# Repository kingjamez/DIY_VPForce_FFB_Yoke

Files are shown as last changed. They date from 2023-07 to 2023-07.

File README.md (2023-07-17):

# DIY VPForce FFB Yoke
This will be a flight control yoke based on the VPForce Force Feedback Motor System. It's not finished, it's barely started. Use any files here at risk of life and liberty!

This can be used as a standard Cessna / Piper style yoke or also easily adapted to use the Cirrus style side yoke. The only difference will be what you attach to the shaft coming out of the device and where you mount it. I think Cirrus drivers will love it.

It's core will be a section of 8020 aluminum extrusion linear rail. 
The roll axis will be direct drive from an 86BLF04 VPForce motor. A honeycomb alpha yoke will be donating it's controls. I hope to use a shift register to have the yoke talk to the VPForce USB interface. 

The pitch axis will be belt or rack and pinion driven from a 57BLF03 VPForce motor. This is TBD since I very  much want this to be as smooth as possible without sacrificing torque. First tests will be standard 2GT-2mm timing belt just like an Ender 3 X-Axis movement. 2nd tests will be 3GT-3mm endless belt. 3rd Test will be rack and pinion using 3D printed gears. The objective is smooth motion (don't want to waste the anti-cogging that is so well implimented by VPForce). All tests will likely utilize the inertia feature in the VPForce software to give smooth pitch motion.

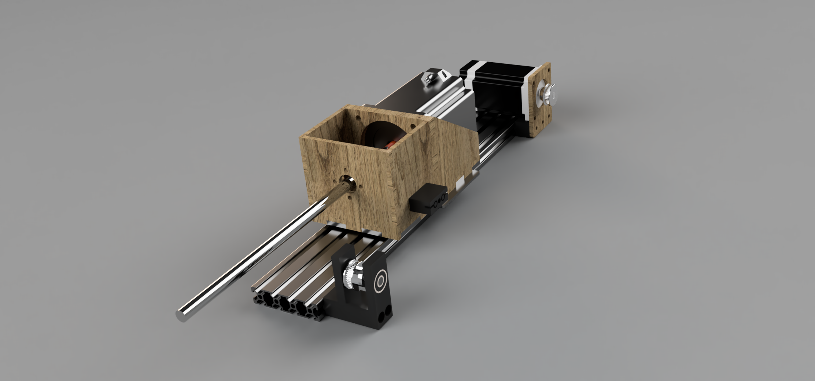
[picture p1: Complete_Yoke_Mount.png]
 

The above box houses the 86BLF04 motor and a shaft coupler to attach the 12mm shaft through a LM12UU linear bearing. This laser cut box will bolt to an aluminum gantry plate and ride along a section of 8020x400mm rail. Here is a link to the rail: https://a.co/d/cz4xqeC 

The gantry plate also came from Amazon but you can cut one out along with the other parts. https://a.co/d/fDJAr2g .
I eventually plan to merge the gantry plate and the bottom of the motor mounting box into one piece. However the width of the 86BLF04 motor matches very well with the location of the holes for the bolts that hold the wheels so I decided to tackle that problem in V2. V1 will require the gantry plate and the motor mount box will just bolt to the gantry plate. 

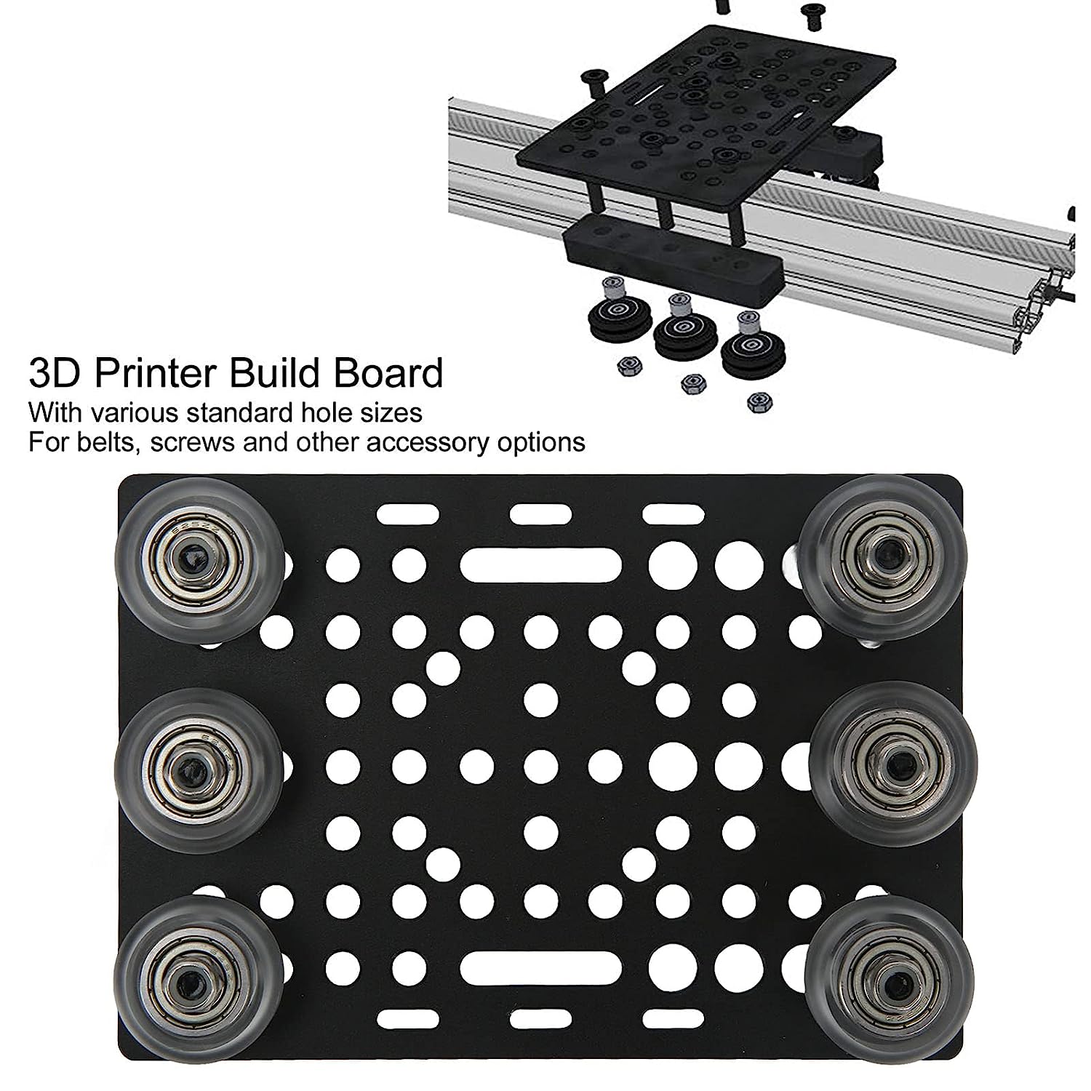
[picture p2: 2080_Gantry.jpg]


This is the 8020 rail: 
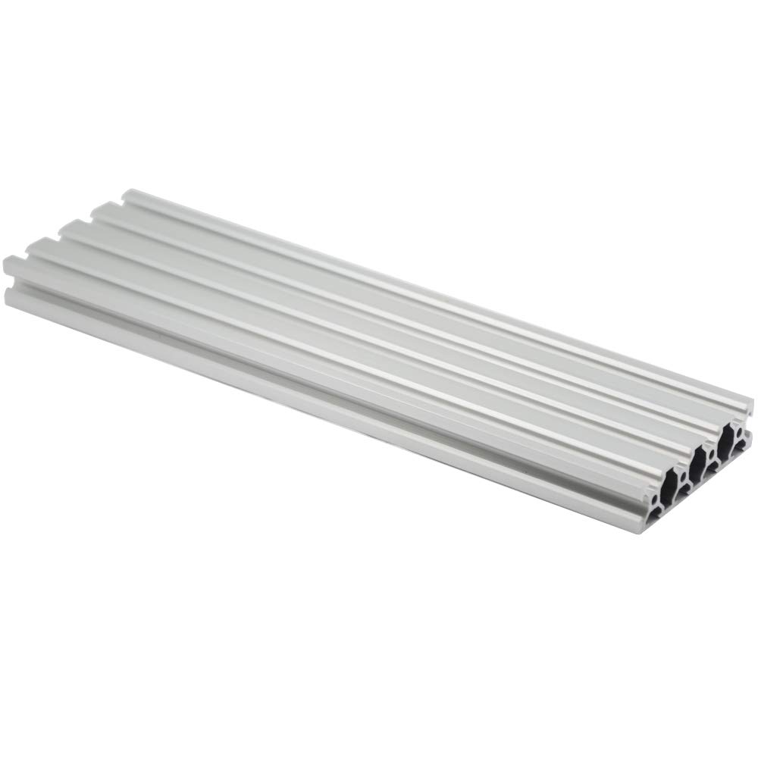
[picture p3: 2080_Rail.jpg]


This project is just getting started, more to come shortly.

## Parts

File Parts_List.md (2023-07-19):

Parts list for FFB Yoke
Motors and motor control board from VPForce:
1x86BLF04, 1x57BLF03, 1x USB control board.
8020x400mm rail. I sourced from Amazon.
Laser cut wood carraige: All DXF's laser cut out of 1/4" (nominal, US 1/4" plywood is 5.35mm) plywood or equivilant. 
3D Printed parts:
1x Rear servo mount
1x Front Idler mount
1x Belt Clamp
1x Belt Clamp nut holder
1x VPForce control board holder

1x Yoke of your choosing. I used a Honeycomb Alpha as a donor. It has a nice yoke that has a 12mm shaft that makes connecting to the 86BLF04 easy.
1x 12.7mm to 12mm shaft coupling to go between motor and yoke shaft.
2x LM12UU Flanged Linear bearings for yoke shaft support.
8x 6mmx25mm bolts for mounting the servo motors.
1x 6mm tap to tap the holes in the 86FLB04 motor to M6 (they come unthreaded).
8x M4x15mm bolts and nuts to secure the LM12UU linear bearings.
2x M5x45mm bolts for the rear servo mount.
2x M5x55mm bolts for the front idler holder.
1x M5x55mm bolt for the belt clamp (this may change)
1x M55 nut for belt clamp.

Wood glue to hold carriage together.
1x 8020 Gantry plate with hardware and 6 wheels. Ensure that it has eccentric spacers for close tolerance rail movement.
4x M4xxx bolts to hold wooden carraige to above 8020 aluminum carriage.

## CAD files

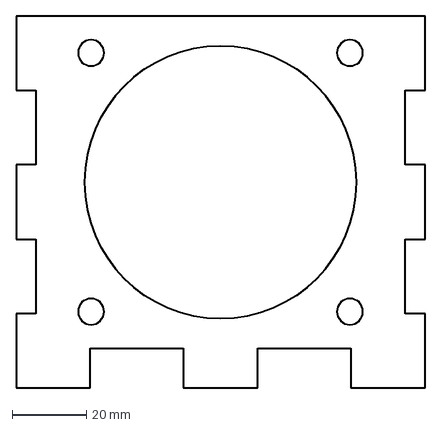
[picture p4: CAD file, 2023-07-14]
dxf/6BLF04_Center_Mount.dxf
110.0 x 100.0 mm

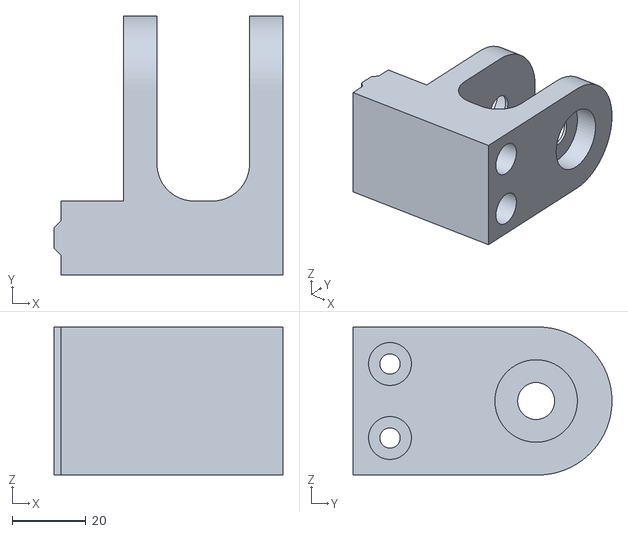
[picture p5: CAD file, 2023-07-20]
STLs/Roller_Pillow_Rail_Mount v7.stl
61.8 x 70.0 x 40.0

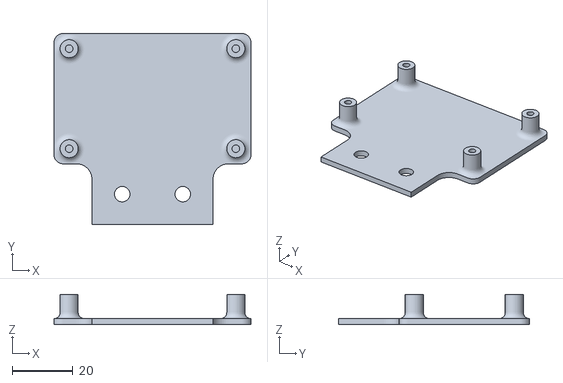
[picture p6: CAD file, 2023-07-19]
VPForce_rail_Board_Holder v3.stl
65.0 x 63.0 x 10.0

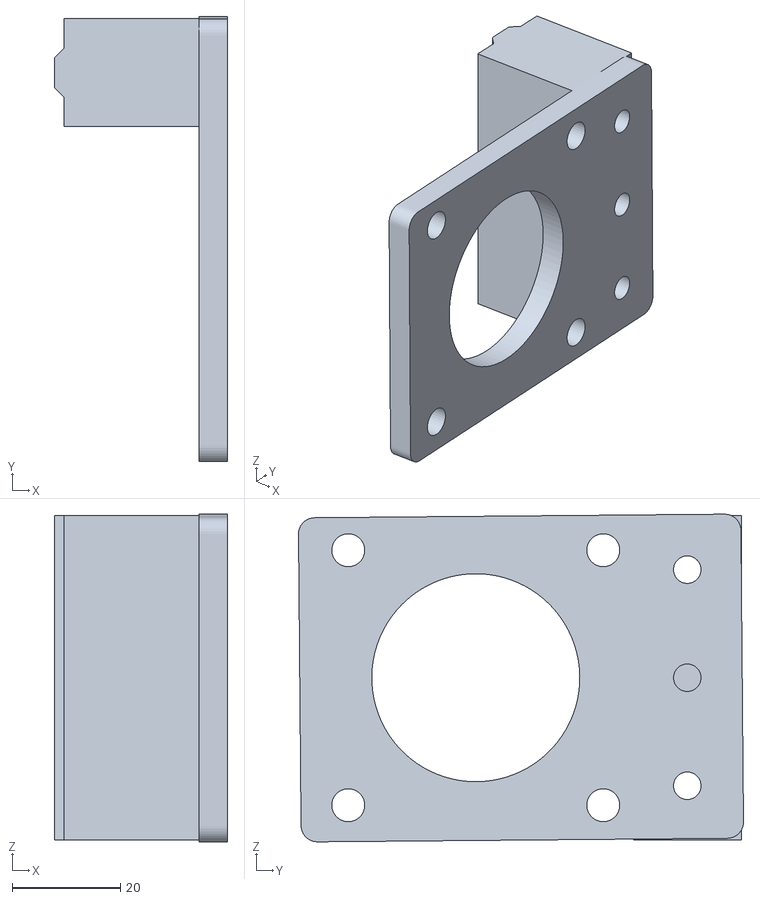
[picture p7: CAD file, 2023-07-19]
Combind_Nema23.stl
32.1 x 82.4 x 60.7

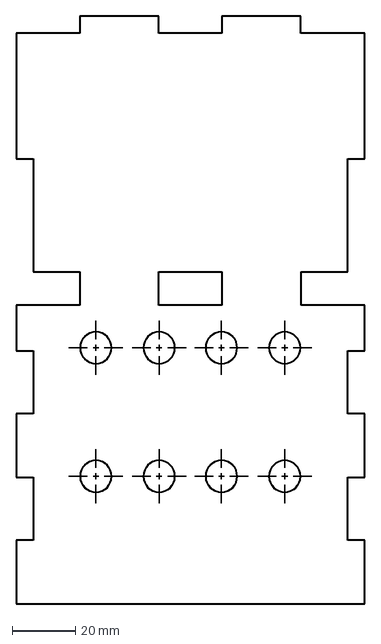
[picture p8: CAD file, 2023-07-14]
dxf/Bottom_Panel_Top_Center_Marked.dxf
110.0 x 185.7 mm

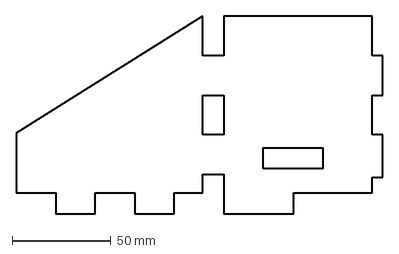
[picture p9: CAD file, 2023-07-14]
dxf/Side_Support.dxf
185.4 x 100.0 mm

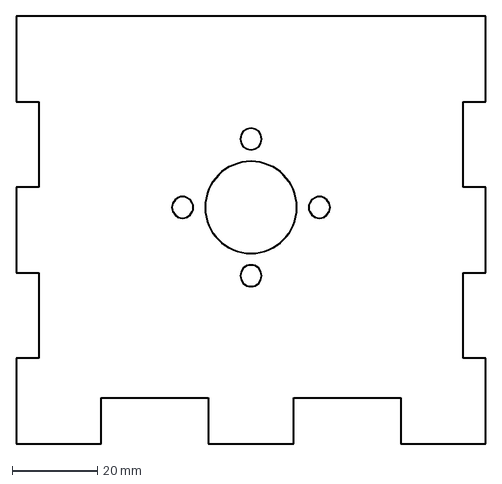
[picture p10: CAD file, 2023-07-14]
dxf/Front_Support.dxf
110.0 x 100.0 mm

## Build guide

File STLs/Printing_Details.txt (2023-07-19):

I printed these out of CF-PETG but I suspect that almost any filament will work well. 
The rear servo mount might benefit from a high-temp filament because that motor gets warm.

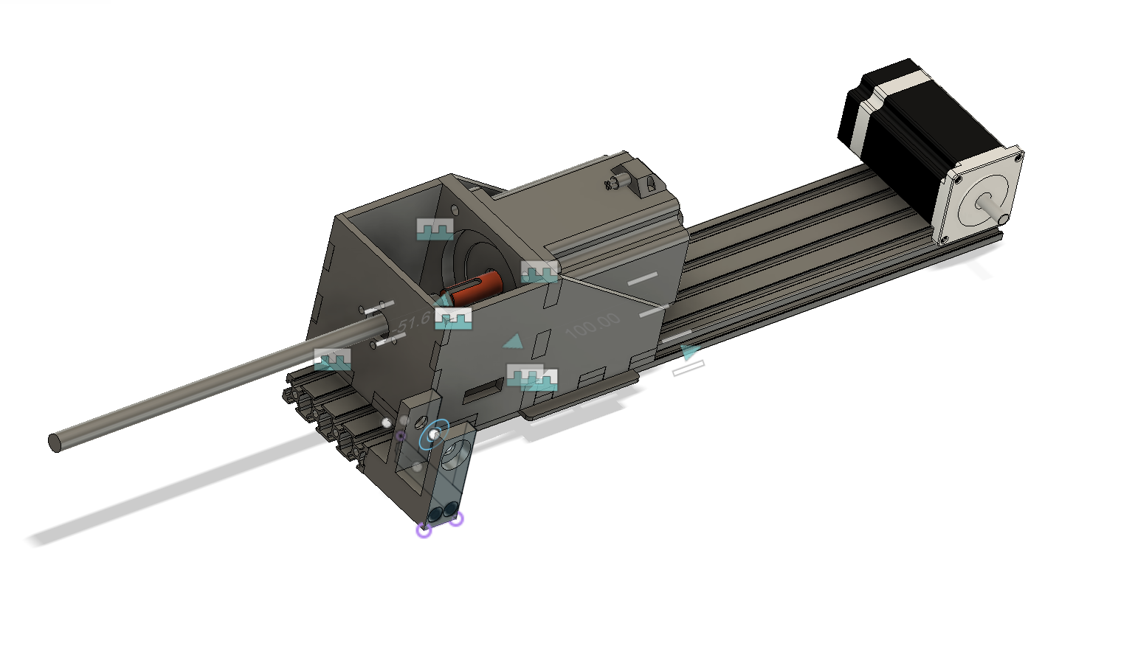
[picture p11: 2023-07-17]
First_assembly.png

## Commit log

2023-07-14 Update and rename 86BLF04_Simplified Drawing v0 Sheet1.dxf to dxf/86BLF04_Center_Mount.dxf
    [6BLF04_Center_Mount.dxf]
2023-07-14 Update and rename Bottom_Panel_Top_Center_Marked.dxf to dxf/Bottom_Panel_Top_Center_Marked.dxf
    [Bottom_Panel_Top_Center_Marked.dxf]
2023-07-14 Update and rename Front_Support Drawing v1 Sheet1.dxf to dxf/Front_Support.dxf
    [Front_Support.dxf]
2023-07-14 Update and rename Side_Mount Drawing v1 Sheet1.dxf to dxf/Side_Support.dxf
    [Side_Support.dxf]
